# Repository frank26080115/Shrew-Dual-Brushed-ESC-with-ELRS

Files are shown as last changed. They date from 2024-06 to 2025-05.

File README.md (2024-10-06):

# Shrew: Dual Brushed ESC with ELRS

Shrew is family of ESCs (Electronic Speed Controller) that can drive two brushed motors, with an ELRS receiver integrated. It is designed to be as small as possible yet still pack plenty of power. It is meant for insect class combat robots.

There are three variations of Shrew

 * Shrew-Pro, for dual brushed motors up to 21A
 * Shrew-Lite, for dual brushed motors up to 3.7A
 * Shrew-Zero, not a ESC, just a receiver

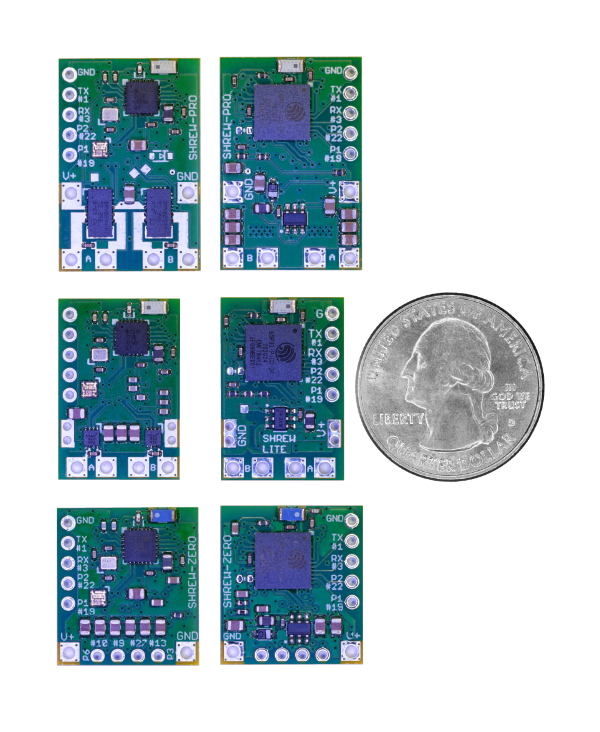
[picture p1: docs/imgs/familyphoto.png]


All of these function as ELRS receivers with 4 or more GPIO pins, capable of controlling other ESCs or servos. These pins can output PWM, as well as better protocols such as Dshot. If you have the skills, you can even use them for I2C and such.

The input voltage ratings of Shrew is incredibly high, even Shrew-Lite can handle up to 36V, that means connecting directly to a 8S battery is not a problem (please see individual detailed specifications).

If you are using AM32 brushless ESCs with Shrew, Shrew features a webpage interface to configure the AM32 ESC. If you have 4 ESCs connected to Shrew, you can change settings on each one individually and test it immediately, all without disconnecting any wires. Plus, you can test the ESCs immediately after making a settings change through the same webpage interface.

## Design Ethos

Safety and reliability is on the top of my priority list

 * Digital protocols are safer than PWM ([why this is better](docs/Digital-Protocols-for-ESC-Control.md))
 * No-pulse failsafe mode by default ([why this is better](docs/No-Pulse-Failsafe-Mode.md))
 * No entering any unexpected modes, there is no way to accidentally enter some sort of calibration mode or binding mode
 * No dead-zone implemented, so there's no control lag at all, and there is also no need for calibration
 * Binding is done with a binding-phrase, extremely good for spare parts management of a competitive robot
 * Power input solder points are intentionally placed farther apart to prevent accidental short circuiting
 * RGB LED on it is indicative of control inputs, not just connection state
 * Top quality TCXO and a ceramic antenna for a balance between high RF performance and durability.

## User Manuals

 * [Shrew-Pro User Manual](Shrew-Pro-User-Manual.md)
 * [Shrew-Lite User Manual](Shrew-Lite-User-Manual.md)
 * [Shrew-Zero User Manual](Shrew-Zero-User-Manual.md)

## Open Source Notes

All of the circuitry is designed using CadSoft EAGLE v7. This is NOT Autodesk EAGLE, but Autodesk EAGLE can open the files.

All the manufacturing data is tailored for JLCPCB's PCBA service.

The firmware in this repo are in binary form only, but the source code for them are on a branch of a fork of ExpressLRS: https://github.com/frank26080115/ExpressLRS/tree/shrew

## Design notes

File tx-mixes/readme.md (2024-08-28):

This is a basic mix setup for a robot being controlled by a EdgeTX RC radio transmitter. It implements a translation between "arcade style" controls to "tank style" drivetrains. It also repurposes the trim adjustments to implement speed limits and rate limits (as opposed to calibrating servos for airplane control surfaces).

The `*.yml` files (for some specific models of radios) I have uploaded can be placed on the microSD card under the `MODELS` directory, rename them to simply `model00.yml` first. Change the number `00` to something else if you need to. If you don't have one of these specific radios, simply take the one most similar to the one you have.

 * [File for RadioMaster MT12](modelnn_mt12.yml)
 * [File for RadioMaster Pocket](modelnn_pocket.yml)
 * [File for RadioMaster Zorro](modelnn_zorro.yml)

To change between using the left stick and right stick, edit the sources in the `inputs` menu.

If you've wired a drive motor backwards, edit the channel direction from the `outputs` menu, select which side and edit the `direction` setting to be `INV`.

Channel 31 and 32 has an `EXPO` curve item set, it's default to 25%. Edit these two curves to fit your needs, 0% means linear.

There are a few logical switches being used by this mix:

 * L57 is the weapon off switch (true = weapon off)
 * L58 is the robot-invert switch, for driving upside-down
 * L56 is the auto-weapon-slow toggle, use this to enable/disable this feature, or temporarily override this feature

The logical switches should be mapped to either phyiscal switches, or be set to a position, using the logical switch panel. (this will make these files more compatible with more radios)

To pick a switch position, set the logical switch to use either `a=b` (true if max) or `a<b` (false if max), with the first parameter being the switch source, and the second parameter being `MAX`. Remember to also set the pre-flight check options for the weapon switch.

There is an intentional slow-up enabled for the weapon channel 3, edit the slowness if you don't need it.

The trim switches are used for real-time adjustments:

 * TrmT, throttle trim: speed scaling for throttle control input
 * TrmE, elevator trim: speed limit for motors, used to scale motor speed up or down after all other calculations
 * TrmR, rudder trim: scaling for steering input, makes the robot turn quicker or slower
 * TrmA, aileron trim: makes one side's motor faster or slower than the opposite side's motor, used to compensate for damaged or binding motor/wheel. If the robot is not driving straight, use this to adjust.

There are a few curves used:

 * CDZ: control dead-zone, implements a dead-zone for the joysticks, can compensate for old joysticks or overly twitchy fingers
   * adjust to fit your needs
 * ADZ: anti-dead-zone, used to avoid any dead-zones implemented on the robot's ESCs, can solve problems with ESCs that appear laggy or unresponsive at low throttle
   * adjust to fit your needs, ask the ESC manufacturer if you have questions
 * P01: positive 0 to 100, a simple line from (-100, 0) to (100, 100)
   * do not adjust
 * P10: positive 100 to 0, a simple line from (-100, 100) to (100, 0)
   * do not adjust
 * WSL: weapon slow, used to automatically slow down a weapon during a steering turn
 * WEP: maps potentiometer/stick to 0 to 100 range, change the range as -100 to 100 if you need to use bi-directional weapon
 * WPS: used by the output stage to apply a offset and multiplication, do not use if the weapon is bi-directional

This mix also includes a control channel for a basic combat robot weapon. Channel 3 is the output for the weapon. Channel 20 is the input for the weapon, using L57 as the switch and potentiometer S1 as the speed control. Channel 3 is set to slowly ramp up the weapon speed, but also brake immedately if the weapon needs to be turned off.

## Notes for MT12

Knob `P2` controls weapon speed, but it is also locked by switch `SA`. This behaviour can be edited.

Weapon speed acceleration has been set to `2.0`, if you want it faster, use the `mixes` page, edit channel 3, change the `slow up` value.

TrmT is T4, TrmE is T3, TrmR is T1, and TrmA is T2

## Notes for Pocket

Knob `S1` controls weapon speed, but it is also locked by switch `SD`. This behaviour can be edited.

Switch `SA` toggles inverted driving mode.

Weapon speed acceleration has been set to `2.0`, if you want it faster, use the `mixes` page, edit channel 3, change the `slow up` value.

## Notes for Zorro

Knob `P1` controls weapon speed, but it is also locked by switch `SE`. This behaviour can be edited.

Switch `SF` toggles inverted driving mode.

Weapon speed acceleration has been set to `2.0`, if you want it faster, use the `mixes` page, edit channel 3, change the `slow up` value.

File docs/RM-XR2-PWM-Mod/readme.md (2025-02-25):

# RadioMaster XR2 Receiver PWM Mod

The RadioMaster XR2 is a nano-sized ExpressLRS receiver. It typically only communicates to a drone flight-controller via two UART pins. Modifying this receiver can allow it to output up to 5 PWM (or even Dshot) signals, which makes it useful for robotics applications.

This is the evolution of the same PWM modification done to many previous generation ExpressLRS nano-sized receivers.

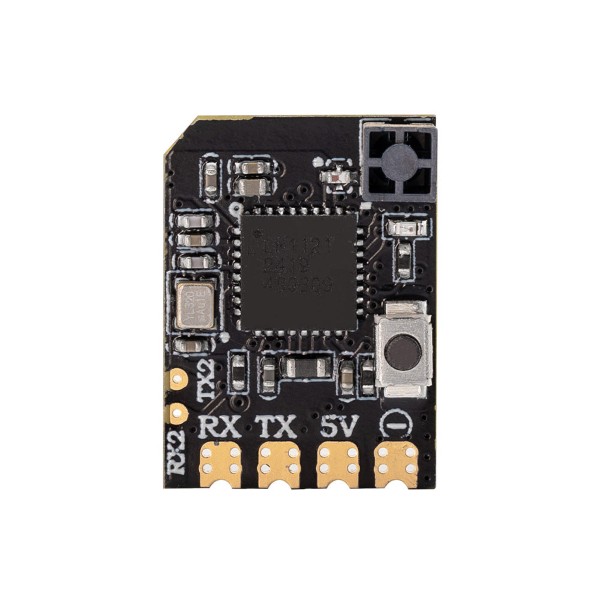
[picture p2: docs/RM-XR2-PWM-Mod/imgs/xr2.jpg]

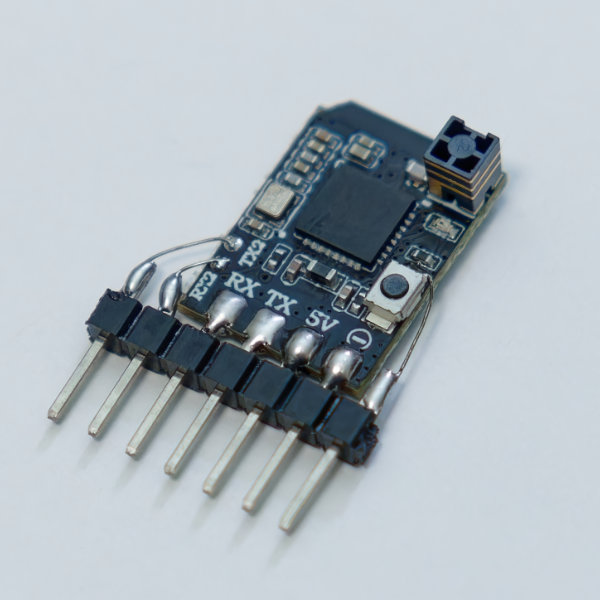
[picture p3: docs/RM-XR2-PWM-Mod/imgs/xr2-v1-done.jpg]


## User Manual

If you have already done the modification, then please read the user manual linked here TODO.

Here's the pin-out for your convenience:

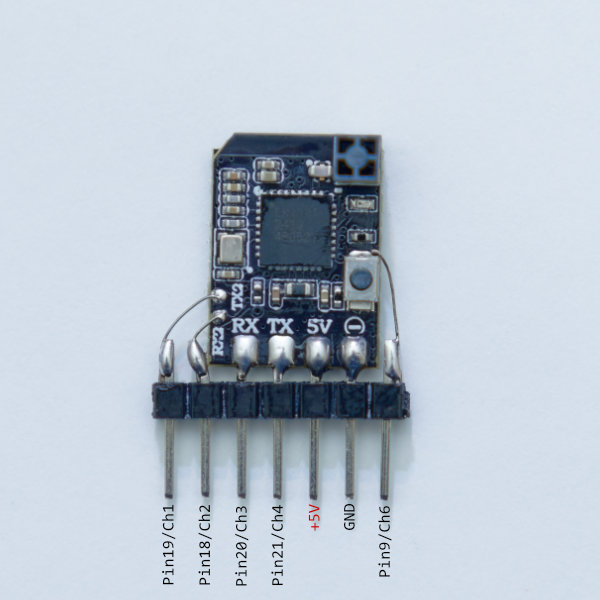
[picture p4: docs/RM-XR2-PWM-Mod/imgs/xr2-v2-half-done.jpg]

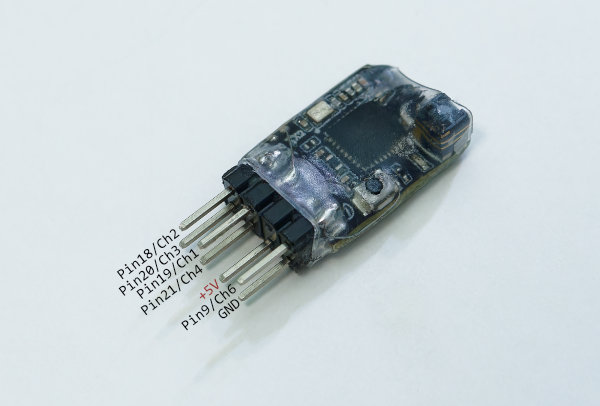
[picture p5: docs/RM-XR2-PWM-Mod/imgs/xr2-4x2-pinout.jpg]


## Method 1: single row of pins

Get a strip of plain male header pins with 0.1" spacing, 7 pins long. Cut and bend the pins according to the photo below:

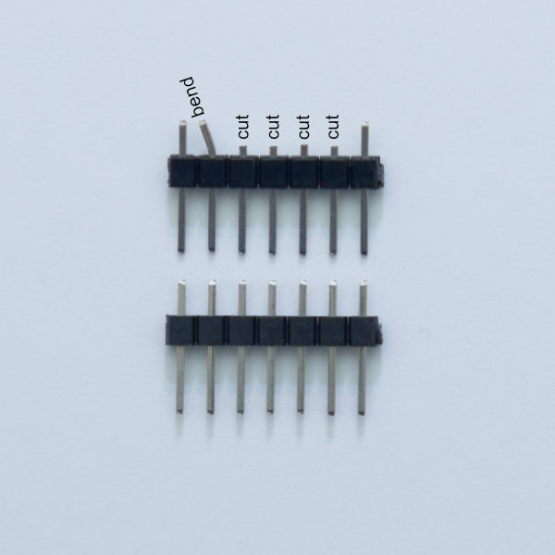
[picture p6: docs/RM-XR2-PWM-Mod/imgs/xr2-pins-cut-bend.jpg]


Solder the header pins to the XR2. Remember to start with just one pin, then adjust it until it is straight, before soldering the four short pins to the castellated pads.

It helps if you stick the male pins into some female headers to keep all the pins straight during soldering. This prevents the pins from moving even if the heat melts the plastic holding the pins.

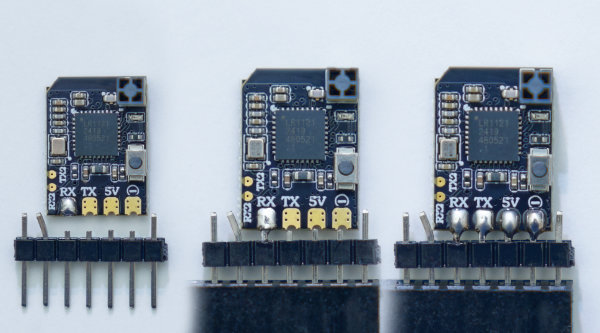
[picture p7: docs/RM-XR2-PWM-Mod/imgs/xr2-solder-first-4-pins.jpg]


Get some thin wire, 30 AWG or 32 AWG solid (not stranded) wire. If you don't have this, maybe take apart some stranded wire and grab individual strands out of it. These wires will only carry a small signal so they don't have to be thick.

Solder one piece of wire to the top solder-pad of the button. The other end of this wire needs to be soldered to the pin on the far right side.

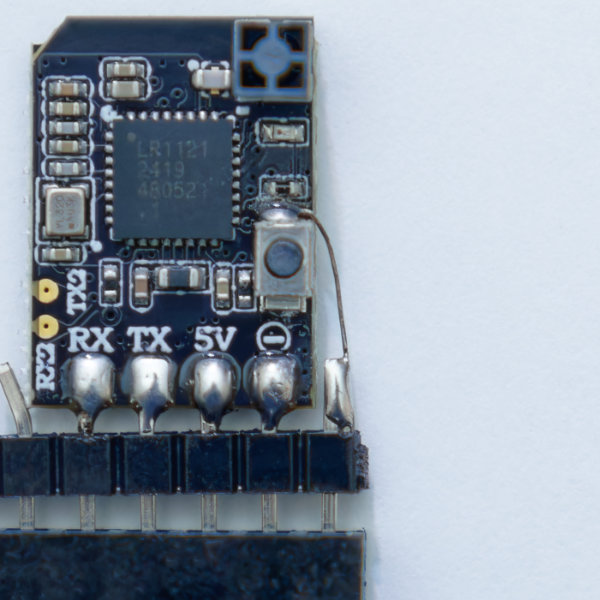
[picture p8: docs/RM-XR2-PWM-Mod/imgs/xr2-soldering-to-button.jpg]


On the left side of the XR2, there are two tiny pads labelled RX2 and TX2. Solder short lengths of wire from those pads to the header pins on the left.

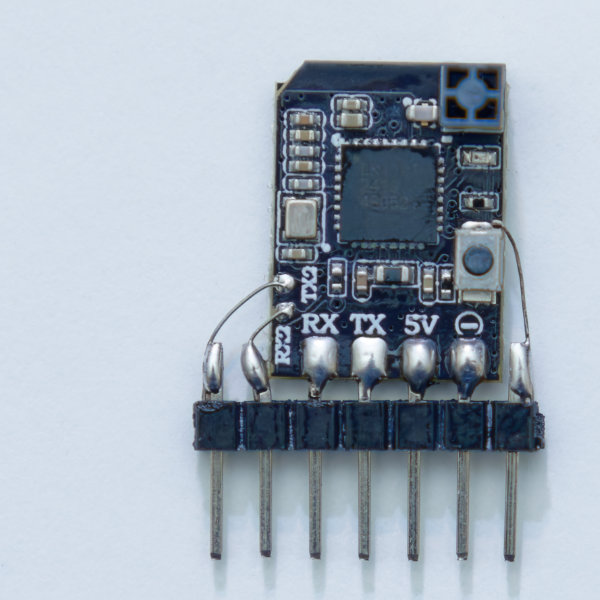
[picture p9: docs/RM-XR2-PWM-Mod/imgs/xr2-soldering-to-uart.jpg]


You are half done. Clean the entire circuit using 99% rubbing alcohol and an antistatic toothbrush. Take a break.



## Method 2: two rows of pins

This method makes the whole receiver narrower. Start by getting a 4x2 chunk of male header pins (0.1" pin spacing). Modify it according to this photo:

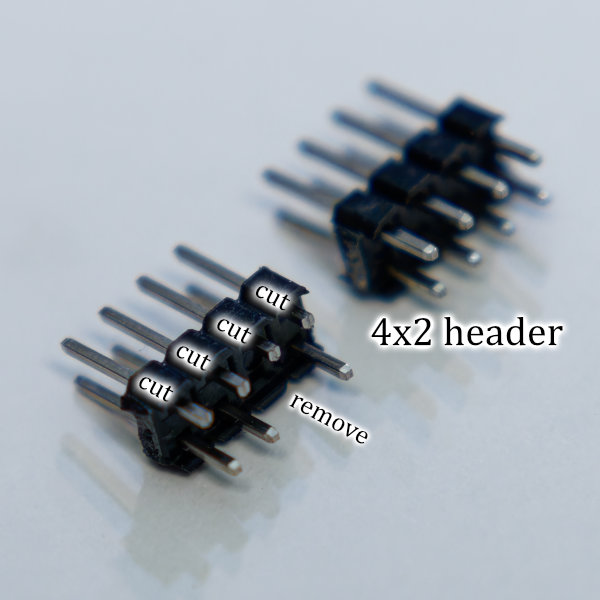
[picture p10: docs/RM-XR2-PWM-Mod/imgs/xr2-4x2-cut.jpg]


Then, similar to the previous method, solder the shorter header pins to the castellated pads on the XR2. The longer pins should be on the higher side.

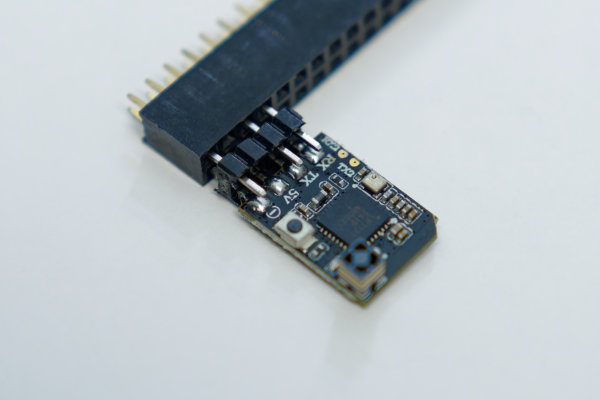
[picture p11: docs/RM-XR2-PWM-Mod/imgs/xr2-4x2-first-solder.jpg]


Make sure there are no unintentional shorts/bridges to the upper row.

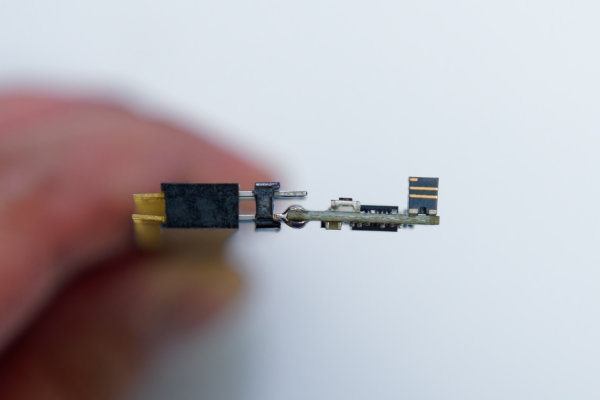
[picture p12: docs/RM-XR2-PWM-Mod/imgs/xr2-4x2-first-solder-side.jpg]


Use thin wire (mentioned above) to connect the top solder pad of the button to the upper header pin on the right side.

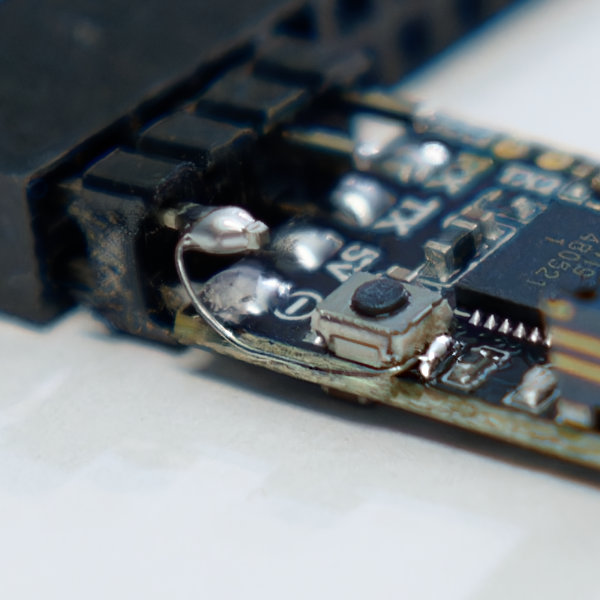
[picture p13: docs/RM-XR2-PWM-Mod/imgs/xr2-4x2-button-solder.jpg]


And then connect the RX2 and TX2 pads to the upper header pins on the left side.

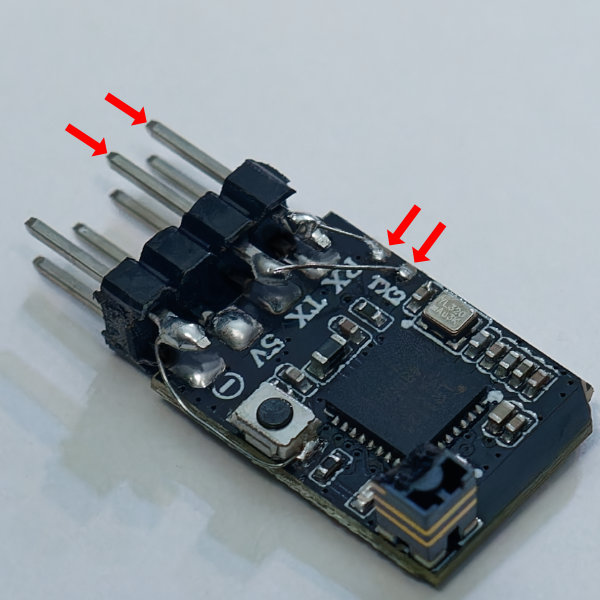
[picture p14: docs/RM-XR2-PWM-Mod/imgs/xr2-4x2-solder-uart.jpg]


Clean the entire circuit using 99% rubbing alcohol and an antistatic toothbrush. Take a break.

## Additional Soldering Notes:

If the wire for the button is too difficult, simply don't attempt it. You will end up with 4 channels instead of 5.

## Protecting Everything

Since we expect this receiver to take a beating, we need to toughen it up because it has a very tall antenna and now some thin wires. Use epoxy to secure the antenna and the thin wires. Then protect everything using heat-shrink tubing.

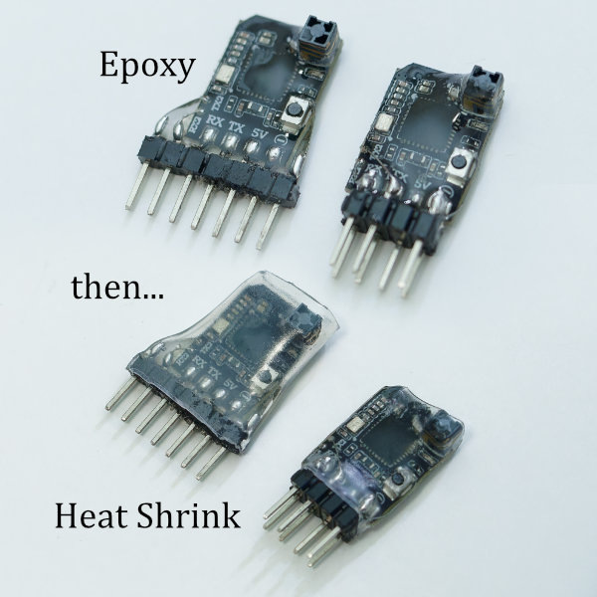
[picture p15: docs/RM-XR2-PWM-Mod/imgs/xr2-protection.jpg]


## Firmware Modification

The real evolution here is that RadioMaster made the XR2 receiver with a more advanced microcontroller, the ESP32-C3. Previous generations of receivers used the ESP8. The ESP32-C3 has more internal features that allows it to send Dshot signals. It can also establish serial communications on any pin, not just the ones labelled as RX and TX.

Dshot is a digital signal that is better than PWM. Since it is digital, it is more resilliant against electrical noise, making it work better with higher voltage power systems.

Since it can communicate using serial on any pin, it means that it can reconfigure AM32 speed controllers (ESC) connected to it, not just one, but as many as you want.

These features are not in the official ExpressLRS firmware yet (today is Feburary of 2025)! Currently Dshot only works with BLHeli32 and not AM32. The AM32 configurator is also not a part of the ExpressLRS project. I have written my own fork of the ExpressLRS firmware that makes Dshot work with AM32 and also adds the AM32 configurator. I have also added a ton of other features specifically tailored towards combat robotics.

Please download the firmware here: [fw-bins directory, pick the latest one](fw-bins)

To update, first get your XR2 into the Wi-Fi mode. Read ["How to get to the Web UI" from this guide](https://www.expresslrs.org/quick-start/webui/#how-to-get-to-the-web-ui).

(Summary: once the receiver is powered ON, wait for 60 seconds until the Wi-Fi interface starts. Connect to the access point named `ExpressLRS RX`, with the password `expresslrs`. There will be no internet available through this access point and your smartphone or computer will need to be told to not disconnect from it.)

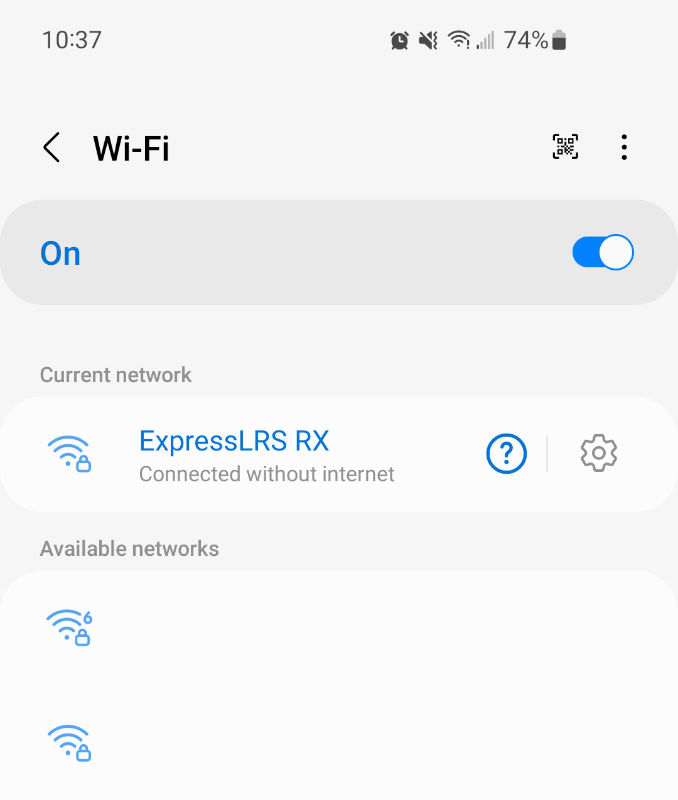
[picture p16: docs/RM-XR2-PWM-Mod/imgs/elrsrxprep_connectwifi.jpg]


Then go to the firmware update tab

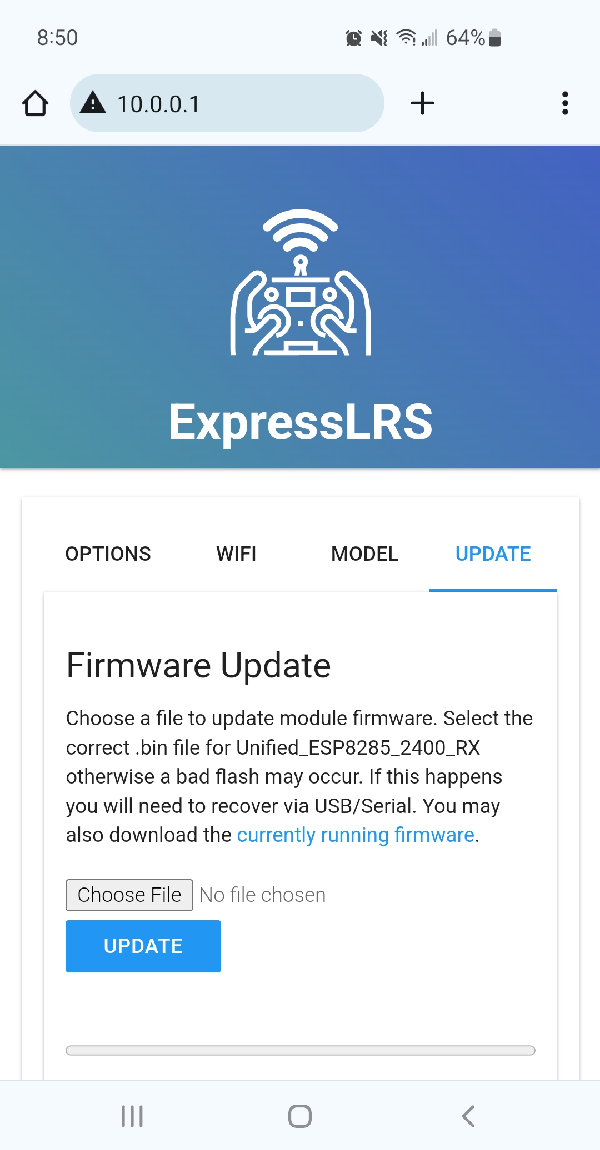
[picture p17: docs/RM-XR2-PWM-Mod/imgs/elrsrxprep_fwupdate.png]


Use it to upload the file I provided. Ignore any warnings and then power cycle.

WARNING: There is bad news, if you own a transmitter that does not support Gemini, then the XR2 is not able to achieve 1000 Hz packet rate, the highest rate will be 500 Hz. If you have your transmitter set to use 1000 Hz, which is the default, then the XR2 will fail to connect.

WARNING: the bind button on the XR2 will not function as a bind button after this mod, so you must bind it with a bind phrase.

List of additiona features that's not in official ExpressLRS release:

 * Dshot works with AM32 and also 3D-Dshot, required for drive motor ESCs that are bidirectional
 * AM32 configurator
 * "Administered" binding mode, prevents accidental loss of binding due to power failure
 * Ability to lock the packet rate to a single frequency, which speeds up the time it takes to reconnect if power is lost
 * Copy settings from one receiver to another
 * Easy for developers to add new features

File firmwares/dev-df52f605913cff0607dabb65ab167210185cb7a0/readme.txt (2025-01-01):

this version adds a boot LED animation that indicates abnormal reasons for reboot

there is also an armed state indication

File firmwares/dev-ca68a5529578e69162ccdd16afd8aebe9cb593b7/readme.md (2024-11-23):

Build from development branch ca68a5529578e69162ccdd16afd8aebe9cb593b7

This version fixes AM32 not responding to DSHOT.

A new DSHOT mode has been added called "Dshot-3D", and it must be used if the ESC is configured for bidirectional rotation (such as for robot drive motors)

Added some minor features to the AM32 configurator:
 * make "complementary PWM" enabled if "bidirectional" is enabled
 * asking if the user wants to switch to/from Dshot-3D if bidirectional is enabled/disabled

Added a mixer for arcade tank drive mixing.

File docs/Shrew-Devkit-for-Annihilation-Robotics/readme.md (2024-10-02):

# Shrew Dev-Kit for Annihilation Robotics

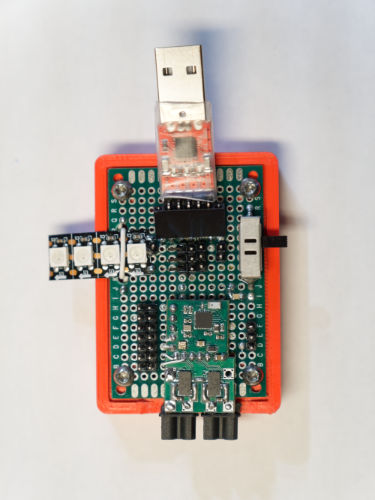
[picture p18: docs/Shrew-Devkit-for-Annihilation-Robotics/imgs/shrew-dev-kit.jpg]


This is a "developer's kit" built using an old retired version of Shrew. It allows for quick repeated updating+testing of Shrew firmware, without having to mess with an actual robot. The serial port is available for updating and debugging. The power comes from the USB port. There are pins that can be connected to external devices.

# Overview

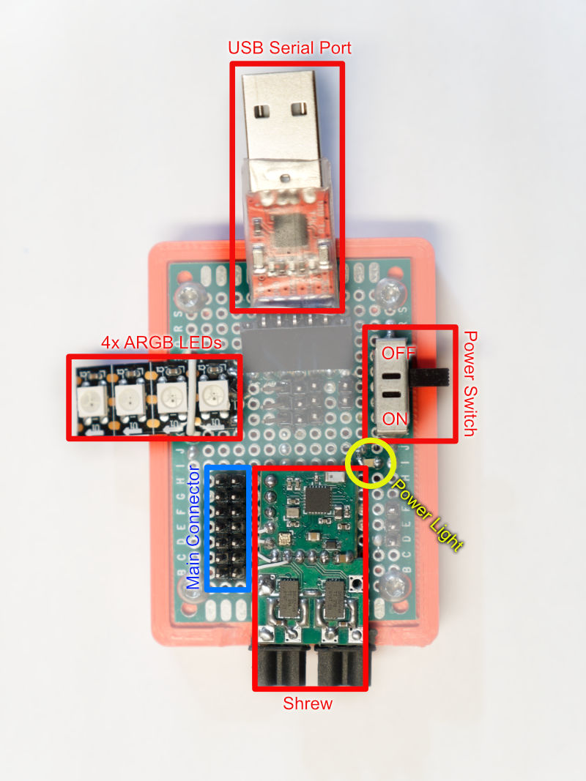
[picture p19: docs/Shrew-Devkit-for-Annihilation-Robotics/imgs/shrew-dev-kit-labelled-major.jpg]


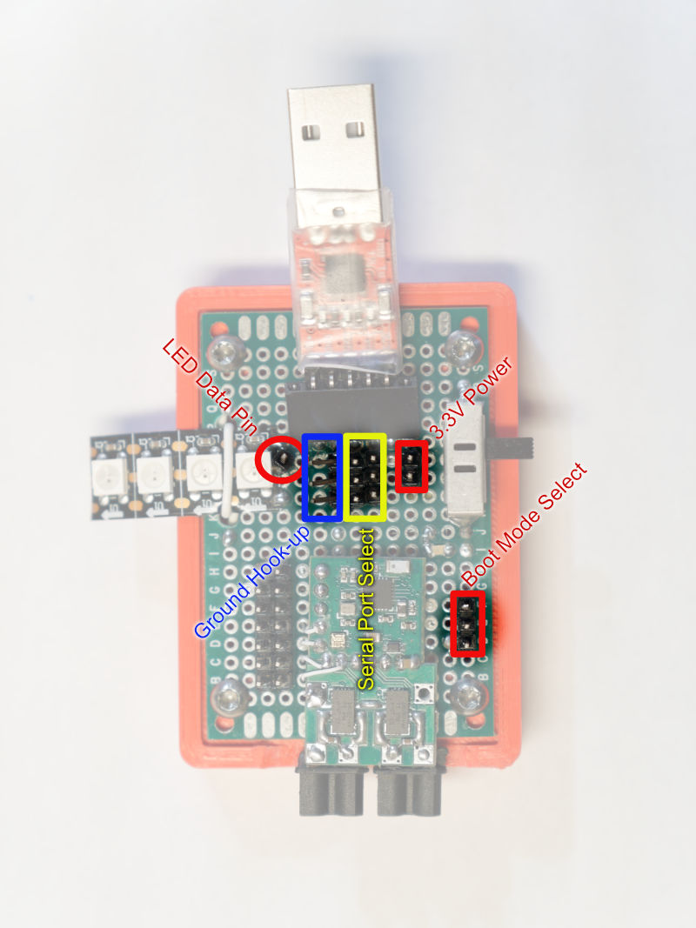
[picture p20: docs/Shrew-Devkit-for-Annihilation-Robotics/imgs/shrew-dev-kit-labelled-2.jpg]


# Pins

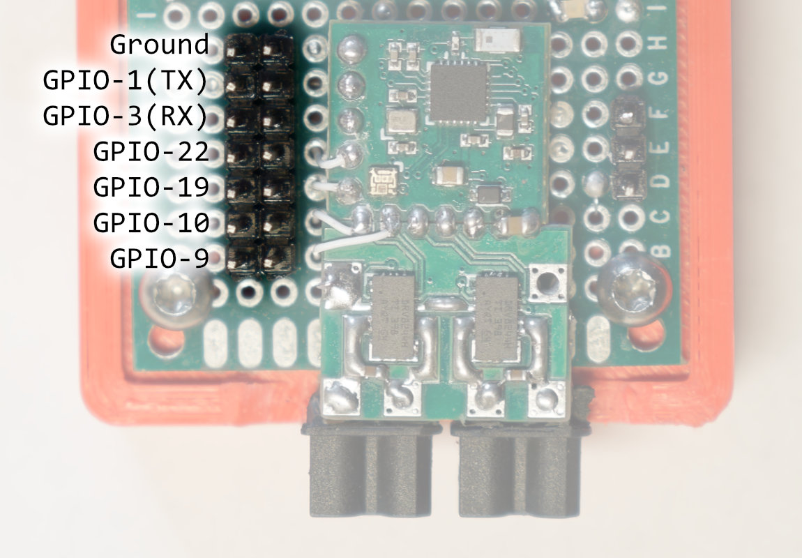
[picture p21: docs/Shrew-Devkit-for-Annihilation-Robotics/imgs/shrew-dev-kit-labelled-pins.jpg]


Each row has two pins, the two are both connected. This can make it easier to connect both an external device and a logic analyzer.

# Shunt Jumpers

Use the included shunt-jumpers to select bootloader mode vs normal mode.

Use the included shunt-jumpers to decide if the USB serial port should be connected or disconnected. If you wish to use the serial port pins for other devices, then move the jumper to the "disconnected"  position so that the USB serial port does not interfer with the external device.

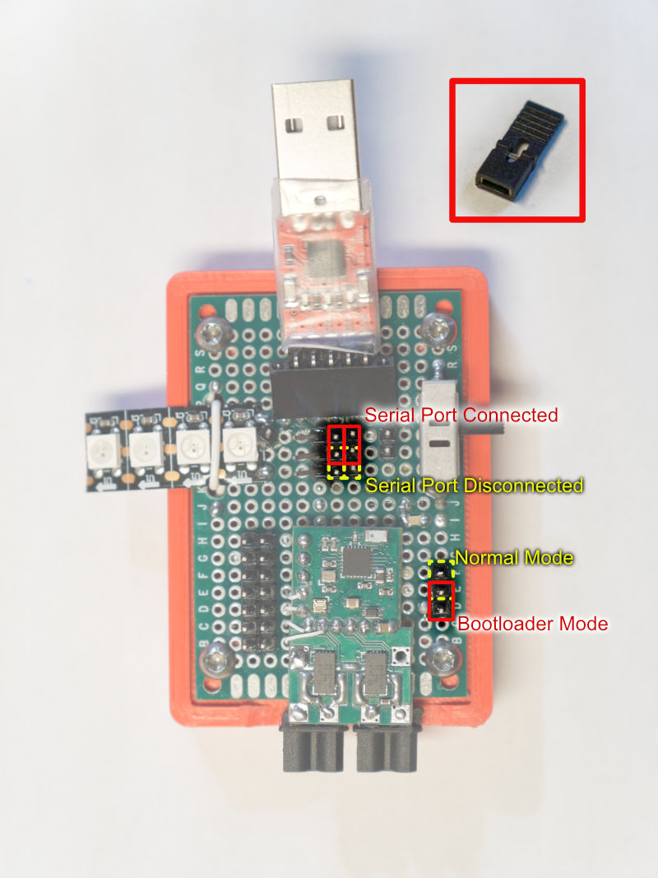
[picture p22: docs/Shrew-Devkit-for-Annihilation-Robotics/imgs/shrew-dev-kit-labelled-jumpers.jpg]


(hint: the yellow positions are meant for you to store the shunt-jumpers so that you don't lose them)

# Using the LED Strip

There is a data pin for the LED strip, use a female-to-female wire to connect that data pin to a GPIO pin on the big main connector. This allows you to pick and choose the pin freely.

# USB Serial port

The connector for the USB serial port is only designed for a particular design I found on Amazon. Please don't lose it. If it needs to be replaced, use this [Amazon product link](https://www.amazon.com/gp/product/B07T1XR9FT/)

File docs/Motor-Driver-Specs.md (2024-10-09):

# Motor Driver Specifications

Shrew-Lite uses DRV8231A motor drivers. Shrew-Pro uses DRV8244 motor drivers. Both of these are integrated H-bridge chips. The datasheets can be [found here (click here)](datasheets-manuals)

## Protection Features

The motor drivers that Shrew uses all feature over-current protection and over-temperature protection. This means, at least according to the manufacturer, they should never allow themselves to be overloaded to a degree that cause them to fail.

Importantly, these drivers also recover from the protected states automatically, and quite quickly.

These protection features are implemented as a shutdown. When the current limit is hit, the chip completely shutsdown, it does not attempt to lower the output to limit the current to a ceiling. Importantly, these drivers also recover from this state automatically, and quite quickly.

The DRV8231A features a very consistent current cutoff, specified at 3.7A. I've tested this with just Gecko motors, which have a stall current only just a little bit over the limit, and it basically refuses to even twitch. This means it's not waiting for much of a "warm up" before kicking in the protection.

The DRV8244's limit is more variable, between 21A and 40A, it is likely temperature dependant. This isn't a bad thing, it allows for more potential performance yet still having a protection when absolutely neccessary. If you analyze the MOSFET resistance of the DRV8244, the variability of the limit might be because it generates such little heat.

If you are building a robot with motors that need the DRV8244s, you will literally melt your motors way before surpassing 21A.

## MOSFET Resistance

All motor drivers have MOSFETs, and while we want to think of MOSFETs as switches, MOSFETs do still have some small resistance. This is actually why MOSFETs heat up when passing current. In fact, this resistance called on-resistance, is probably the most enticing specification that people shop for.

Think about it, the current limit of a MOSFET is actually just a number that will let a MOSFET stay cool enough to survive. The on-resistance is the only thing that causes a MOSFET to heat up. The on-resistance and the ability for the MOSFET to transfer heat away are the two things that dictate what the current limit is. They are all related.

This resistance will also drop the voltage slightly as the current passes through. Your motor will get less voltage after this resistance, which means the motor is weaker. You want the least amount of MOSFET on-resistance to get the best performance out of your motor.

### Example Calculation

Pretend we are using a 12V power source, a motor that draws 3A of current at 12V, and the DRV8231A.

DRV8231A has a on-resistance of 600mΩ

The motor specs suggest its windings have a resistance of 4Ω

The total is 4.6Ω, and when you apply 12V of power and turn the motor driver on, the total current is `12 / 4.6 = 2.6`, 2.6A

Through the MOSFET, that 600mΩ is resulting in, `2.6 * 0.6 = 1.57`, 1.57V loss of voltage going to the motor. Also, it is wasting, `1.57 * 2.6 = 4.08`, 4.08W of heat.

Now, upgrade to a DRV8244, which features a 47mΩ on-resistance (Excuse me? It's that low? YES! This chip represents a technological leap in MOSFET manufacturing technology)

The total current is `12 / 4.047 = 2.965`, 2.965A

The loss through the MOSFET is `2.965 * 0.047 = 0.14`, 0.14V. And the wasted heat is `0.14 * 2.965 = 0.41`, 0.41W.

This means the DRV8244 can give you 13% more torque and speed than the DRV8231A when using the same motors and same input voltage.

This also means you can drive a motor roughly 10x more powerful with the DRV8244 and still get the same heat output as a DRV8231A. The DRV8244 is bigger physically as well so it can handle more heat because of that too.

For fun, consider the L298N motor driver, which was popular when I was a kid, and is still being sold today. It uses classic BJT transistors internally instead of MOSFETs. It's specified to handle 45V inputs and a current of 4A, which is quite respectable on the surface. But if you read the datasheet closely, you'll see that the on-resistance is about 2Ω, which is insanely high. Motors will run much slower with it and the driver is gigantic physically to dissipate the wasted heat.

Despite me raving about the DRV8244's advantages, the DRV8231A is not bad, it's quite good for its size and its price. It's lovely compared to the junk you might encounter that don't tell you what motor driver you are actually getting.

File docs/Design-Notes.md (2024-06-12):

# Microcontroller

The ESP32-PICO-D4 chosen, because ExpressLRS supports it. The AnyLeaf designs uses it https://github.com/AnyLeaf/elrs-hardware/

It has internal flash memory and no PSRAM.

The circuit design has taken into consideration all of the pin bootstrapping.

The SPI bus used to connect the SX1280 uses arbitary GPIO pins selected for convenience during PCB layout. Research indicated that the ESP32 can map any pin to any SPI bus function as long as only one SPI bus is being used. (if both VSPI and HSPI are being used, then you must use the specific pins assigned to both VSPI and HSPI)

The RF antenna is attached directly to the ESP32 LNA pin without any filtering or matching circuit. This is because the Wi-Fi functionality of the ESP32 is only used during reconfiguration and it will always be in close proximity to the user's smartphone.

# Radio

`SX1280IMLTRT` is used, because it is pretty much the only thing used for ExpressLRS in the 2.4GHz band.

It is configured to use DC-DC power mode, not the LDO mode. I have not found any example designs using LDO mode and I also don't see any advantage to using LDO mode.

`2450FM07D0034` is an all-in-one ceramic filter connected to the SX1280 before the antenna.

The SX1280 requires a 52MHz oscillator, ideally a temperature compensated one. The Seiko Epson `X1G0054410320` has been selected due to it's low cost and small size.

RF performance is not super critical. Most ExpressLRS receivers are meant for long range aircraft flight. For combat robotics, the range required is only a few feet at most.

# Motor Driver: DRV8231

`DRV8231ADSGR` is a tiny motor driver capable of up to 3.7A of current and can handle 33V of input voltage.

It features overcurrent protection. When the current limit is hit, it will disable itself for 3 milliseconds. It also features undervoltage-lockout and thermal shutdown.

Either the DRV8231 or the DRV8231A can be used in the design as current regulation is not being used at all.

https://www.ti.com/product/DRV8231A

https://www.digikey.com/en/products/detail/texas-instruments/DRV8231ADSGR/15854016

# Motor Driver: DRV8244

`DRV8244HQRYJRQ1` is capable of driving 21A of current and handle up to 35V of input voltage. The internal resistance of this driver is incredibly low at about 47 milli-ohms. In theory, this driver will run cooler than the DRV8231 for my use case.

The QFN footprint is selected. And the HW variant is chosen so that a SPI bus is not required for configuration.

This driver features over-current protection and over-temperature protection. It is configured to automatically retry when a fault is detected. The retry time is under 1 millisecond.

https://www.ti.com/product/DRV8244-Q1

# Voltage Regulator - Mini

`AP7375-33Y-13` https://www.digikey.com/en/products/detail/diodes-incorporated/AP7375-33Y-13/20371309

Rated for 45V and 300mA. Features thermal protection.

I don't expect any users to exceed 18V.

# Voltage Regulator - Mega

`LT1129CST-3.3#PBF` https://www.digikey.com/en/products/detail/analog-devices-inc/LT1129CST-3-3-PBF/889181

`MIC5239-3.3YS-TR` https://www.digikey.com/en/products/detail/microchip-technology/MIC5239-3-3YS-TR/1030750

These LDO voltage regulators have a decent rating and also require low valued ceramic capacitors.

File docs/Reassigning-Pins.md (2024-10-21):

# Assigning PWM to Serial Pins

Shrew comes with serial RX and TX pins assigned to work as a CRSF port by default. These pins can be reassigned to be more PWM or Dshot pins.

There are two ways of doing this, the easiest way is to edit the hardware configuration through the Wi-Fi interface. Activate Wi-Fi mode (see your specific user manual), connect to it, and then visit the page at `http://10.0.0.1/hardware.html`

On this page, you'll see pin function assignments that can be edited with a text-box. Find the `RX pin` and `TX pin` text-boxes, and delete their contents, make sure they are blank. Then, find the text-box for `PWM output pins`, and add the numbers `, 1, 3` to the list.

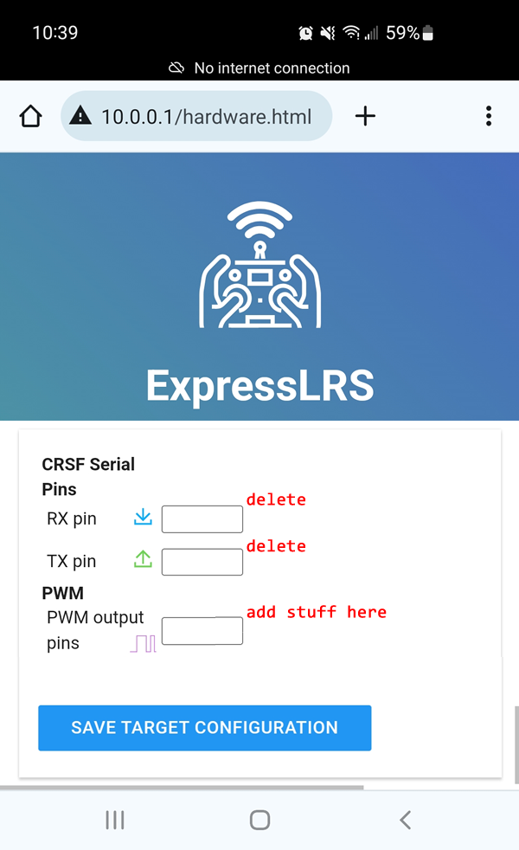
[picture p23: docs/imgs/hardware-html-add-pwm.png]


Save your configuration, and then reboot Shrew completely.

When Shrew powers up again, activate Wi-Fi mode again, connect to it, and then visit the main page at `http://10.0.0.1/`. Now is the time to make sure the PWM channels are configured correctly.

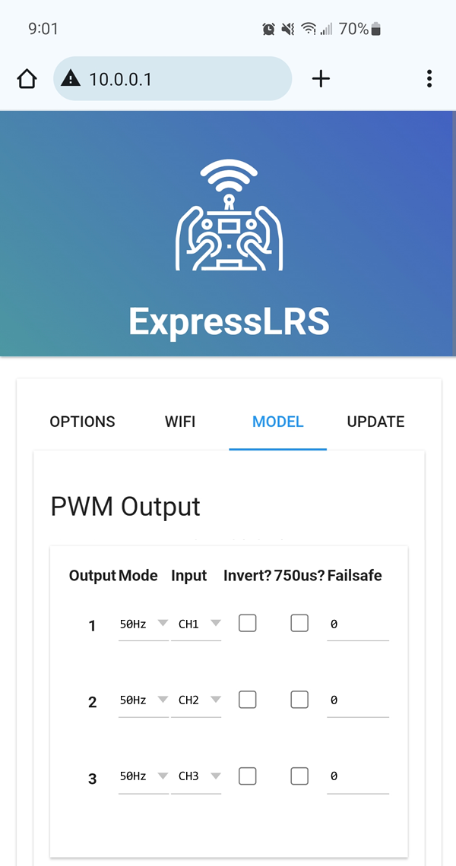
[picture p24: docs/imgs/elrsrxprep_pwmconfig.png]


Make sure to save at the end.

**IMPORTANT:** If you want to change a PWM pin back into a serial pin, make sure you remove it from the list of PWM pins. If you are doing some advanced hacking, you probably don't want your pin to exist in any of the lists where it's not supposed to be in.

## The Other Method

Read the [development guide](Development-Guide) to see how to edit the hardware JSON files, which will become a part of a new firmware file if you rebuild the firmware. The entries in the JSON file for `serial_rx` and `serial_tx` must be blank, and then the pins `, 1, 3` must be added to the `pwm_outputs` array.

## Other Pins

The bootloader mode activation pin is pin 0, and it actually can be used as an output pin.

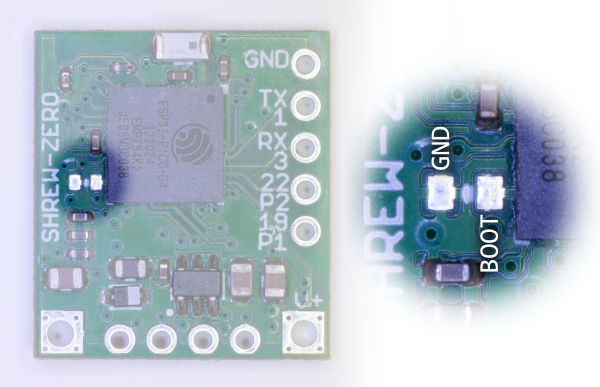
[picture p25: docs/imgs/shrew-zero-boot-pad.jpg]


However you must be careful that whatever you connect doesn't cause the bootloader mode to be activated unintentionally. This means, whatever is connected to this pin must be either pulled-up or floating (aka high-Z or high-impedance).

On a Shrew-Pro, there is a pad to access the reset signal for the SX1280 and DRV8244.



This is pin number 21. You cannot modify this pin's function but you can take advantage of its reset pulse. It will always pulse a low signal for exactly 10 microseconds when the ESP32 is initializing.

## 3.3V Power

You can obtain a source of 3.3V power by soldering to this capacitor:



(this capacitor exists on all variations of Shrew)

The power supply is not very powerful, the rating of the voltage regulator is about 600mA, you should assume that Shrew already uses about 100mA during normal operation, and 250mA during Wi-Fi mode.

You can use this to implement a small IMU sensor as an example.

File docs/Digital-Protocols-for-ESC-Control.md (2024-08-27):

# Digital Protocols for ESC Control

## Understanding PWM

Traditionally, RC radios sent control signals as pulses. A long pulse tells a motor to speed up, while a shorter pulse tells the motor to slow down or stop.



This is called Pulse Width Modulation, or PWM. This was the standard because the RC radio hobby is older than computers, and this was the easiest, cheapest way.

But this type of signaling has many disadvantages. It is an analog form of communication, not digital. The device generating the pulse might have wanted to generate a pulse that's 1.234 milliseconds long, but because of non-idealities of the real world such as temperature and stray capacitance, it might've generated a pulse that's actually 1.235753 milliseconds long. The device reading that pulse is also subject to non-idealities, and read the pulse as 1.237598 milliseconds.

This isn't such a big deal since we have techniques such as trimming, and it is also why almost all ESCs have a calibration function. But these methods do not solve the problem of having noise in the PWM signal.

Below is a simple diagram to illustrate how some noise can cause a motor to unintentionally start spinning, which is a safety concern.



Next, this scenario will make a motor to stutter while it is spinning.



The motor ESC that's reading the PWM signal cannot really distinguish between what is noise and what is a true signal.

## Digital Signals

When a signal is called digital, it means that the information is being sent as **discrete** symbols. When the transmitter sends 123, the receiver receives exactly 123. In that example, the number 123 is encoded as a series of binary bits, ones and zeros, 1 and 0.

These binary bits are still being sent as electrical pulses.

The Dshot protocol sends the 1 bit as a long pulse and the 0 bit as a short pulse. The difference between a long pulse and a short pulse in this context is quite large so it is extremely difficult to confuse between a 1 and 0.



The CRSF protocol is following a standard serial port encoding. 1 is sent as a high voltage and a 0 is sent as a low voltage. The bits are sent in series, each bit taking the same time no matter what. The receiver has to simply read the voltage at regular time intervals. The first bit is always 0, and the last bit is always 1, and the number of bits is always 8. This way, the receiver knows when to start reading.



## Data Integrity Checks

While digital protocols are very resistant to things like temperature changes, they are not immune to noise. Depending on the strength of the noise, a 0 can be turned into a 1.

Digital protocols like DShot and CRSF feature a data integrity check, implemented as a CRC (cyclic redundancy check) checksum. Data integrety checks are what's used to ensure a packet of data, or a file, is not corrupted. The checksum bits are sent after the data bits, and represents a mathematical calculation that can prove the data bits have not been corrupted.

For example, let's pretend to use a protocol that sends 4 numbers and uses 1 number as a simple checksum that sums up all four numbers. We send `34, 57, 19, 24` as the data, 34 + 57 + 19 + 24 = 134, so the final packet looks like `34, 57, 19, 24, 134`. But if because of noise, the 57 is corrupted into 58, then the receiver reads a packet that looks like `34, 58, 19, 24, 134`. The receiver performs a checksum calculation 34 + 58 + 19 + 24 = 135, since 135 is not 134, the receiver knows that the packet is corrupted, and it is ignored.

NOTE: the CRC checksum algorithm is a bit more complicated than just addition.

The data integrity check feature is extremely good for safety and reliability. The diagrams below shows what happens if the noise occurs between packets, or even during a packet.



If the noise happens when no packet is being sent, the noise does not look like a packet with a correct checksum, so nothing bad happens. If the noise occurs right in the middle of a packet, the packet is also simply rejected, due to a bad checksum, instead of causing the motor to behave unexpectedly.

As a reminder, if the noise happens to a PWM signal, it might appear as a longer PWM signal than what it should be, causing a motor to spin up unexpectedly.

Therefore, it is much safer to use a digital protocol that has a data integrity check, such as DShot or CRSF.

## The Relevant Protocols

The most relevant digital protocols for us are: DShot, CRSF, and SBUS. These are used in RC hobbies such as multicopters. Shrew is here to also use these protocols for RC hobby robotics.

### Dshot

DShot is used to control a single ESC. When hobby multicopter microcontrollers (flight controllers, aka FC) became more capable, DShot was invented to provide more precise and more reliable control of brushless motor ESCs.

On Shrew, all pins can be configured to use DSHOT300, where the 300 indicates the bit-rate. This protocol is accepted by all BLHeli_S, BLHeli_32, and AM32 firmware ESCs.

There are no extra configuration needed on the ESCs to use DShot, it should be automatically detected.

Because each DShot signal only connects to one ESC, when Shrew is connected to multiple ESCs with DShot, each ESC can be individually configured through the web-ui. When using Shrew, DShot is the recommended method of connecting to ESCs.

### CRSF

CRSF is a protocol used to communicate between a RC radio receiver and a flight controller, the flight controller is expected to take data from a CRSF packet, and then split it to DShot packets for the four ESCs typically used in a quadcopter. But today, ESCs running AM32 can decode CRSF directly instead of requiring a flight controller.

(NOTE: only the cutting edge experimental AM32 firmware can decode CRSF right now, the official regular AM32 firmware cannot, we are all waiting for the experimental features to be added to the official features. It is easy to upgrade older AM32 firmware to the newer experimental firmware)

A CRSF control packet can carry multiple channels of data at once. This means one output pin on the receiver can control multiple ESCs at once. This requires each ESC to be configured to use CRSF and also configured to know which sub-portion of the whole CRSF packet it should be reading.

Shrew sends CRSF out the UART-TX pin by default. This pin can be reassigned as a PWM or DShot pin if you don't need it.

Because while using CRSF, all the ESCs have to use a single pin, the ESCs **cannot** be configured at all while connected to the receiver.

### SBUS

SBUS is similar to CRSF, it is the standard used by FrSky brand products. ESCs running the latest BLHeli_32 firmware can decode SBUS. FrSky intentionally made SBUS difficult to use by DIY electronics hobbyists, in order to drive more sales of their own products. Hence it is not as popular.

Shrew is capable of sending SBUS. The protocol needs to be reconfigured from CRSF to SBUS through the web-ui. The baud rate also needs to be changed to 100000.

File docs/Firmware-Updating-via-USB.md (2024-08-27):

# Firmware Updating via USB

## Preparing the Circuit

The Shrew circuit has a `BOOT` pad on it, next to it is a ground pad.



To place it into bootloader mode, solder something between the boot pad and the ground pad. It's quite easy to bridge the two pads with just a single blob of solder, but an alternative is to use a thin piece of wire.



## USB to Serial Converter

You will need to have a USB-to-serial converter of some sort.



There are a lot of options. My personal preference is to get something from SparkFun Electronics

 * [SparkFun Serial Basic Breakout - CH340C and USB-C](https://www.sparkfun.com/products/15096)
 * [SparkFun Serial Basic Breakout - CH340G](https://www.sparkfun.com/products/14050) (USB-micro)
 * [SparkFun Beefy 3 - FTDI Basic Breakout](https://www.sparkfun.com/products/13746) (this one claims to handle more power on the 3.3V bus, but costs 2x as much)
 * [Amazon product link](https://www.amazon.com/dp/B07T1XR9FT) (it's a pack of 4 for about $10)

For whichever one you get, plug it in to your computer and install the appropriate driver for it.

If the voltage on the converter can be changed, make sure it's set to 3.3V

## Connections

**IMPORTANT:** make sure the boot pad is already grounded!!!

Make the connections like so



Notice that the TX pin on the converter connects to the RX pin on the Shrew. The RX pin on the converter connects to the TX pin on the Shrew.

## Flashing

If you are using the online firmware configurator tool at [https://expresslrsconfig.eleccelerator.com/](https://expresslrsconfig.eleccelerator.com/) then you should be able to click "Flash Firmware". You will be prompted to select a serial port, select the one representing your USB-to-serial converter.



If you are using PlatformIO (if you are building from source code), then get to the PlatformIO tab, select `Unified_Shrew..._via_UART` as appropriate, select the serial port at bottom of the screen, and then click `Upload`.





**IMPORTANT:** if you need to do a recovery of some sort, it might be wise to also perform a full flash erase. For PlatformIO, the option for `Erase Flash` is tucked under the `Platform` option group.

**IMPORTANT:** Do not use the official ExpressLRS configurator. It does not provide the customized firmware version that Shrew requires.

## Remove the BOOT Jumper

After you finished flashing, remember to remove the solder jumper you put on the `BOOT` pad. Or else the Shrew will never power up into normal mode, it'll be stuck in bootloader mode until you remove that jumper.

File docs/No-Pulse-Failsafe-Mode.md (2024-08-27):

# No-Pulse Failsafe Mode

ExpressLRS features a failsafe mode called "no-pulse", which means that if the radio transmitter is disconnected somehow, the ExpressLRS receiver sends absolutely no signals to connected ESCs at all.

This is different from other RC radio receivers, where you set a specific pulse width that is to be sent when the radio transmitter is disconnected. This is called "set position" inside ExpressLRS, as ExpressLRS allows you to pick between three different failsafe modes.

The "set position" failsafe mode is not very safe when it is used in a hobby robotics context.

First, understand that ESCs typically require an **arming** signal before it will spin a motor. The arming signal is a signal that tells the ESC to stop spinning. This is supposed to ensure that the motor never starts spinning as soon as the user turns on the power switch. If the user left the throttle on the radio transmitter in a high position, and then powered-on the robot, it does not immediately start spinning the motor.

The problem is if the failsafe signal is also the stop signal, then that means the failsafe signal is also the arming signal. Disconnecting a radio transmitter will also arm the ESC, maybe without the user even realizing. If the user powers-on the robot but leaves the radio transmitter off, then the receiver will arm the ESC, and then if the user powers-on the radio transmitter next with a high throttle, then the motor will unexpectedly start spinning.

In contrast, when a no-pulse failsafe mode is used, then the **ESC will never arm unless both the radio transmitter is already powered-on and also the throttle is actually low**. And if the signal is lost, the **ESC will go back into an disarmed state**, waiting for another arming signal.

Also, with bidirectional ESCs using PWM, it is possible for high temperatures to cause the failsafe position to actually be misinterpreted, and then the motor will unexpectedly start spinning with no way of shutting it down. The no-pulse failsafe mode will prevent such incidents from happening.

While it is possible to configure most radio transmitters to warn the user if the transmitter has a high throttle when booting up, it is simply not reliable to expect the user to... actually do anything, even getting a user to read a manual is pretty hard (thanks for reading, by the way). These are also often kids. Thus, the Shrew is configured to use no-pulse by default.

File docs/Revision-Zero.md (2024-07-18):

# Revision Zero

The first batch of prototypes were made around June of 2024. This batch is special and different from subsequent batches.

All PCBs are made without castellated edge holes to save cost. This makes the PCB a bit bigger than intended. To join the receiver and motor driver PCBs together, the edge of the PCB can be sanded down first to create castellated edge holes that are soldered together.



The receiver PCB half is manufactured as a standard 4 layer PCB with 1 oz copper. The mini motor driver PCB is made with a 2 layer PCB with 1 oz copper. The mega motor driver is made with a 2 layer PCB with 2 oz copper. Any future revisions with the two halves integrated will need to use a 4 layer PCB.



I forgot to put some silkscreen text on the PCBs. Please refer to diagram to avoid any wiring mistakes.

The footprints being used for the 0402 components are a bit larger than what the PCB manufacture prefers, but this might help me when I am hand soldering or doing repair work. Future revisions will have a smaller footprint for the 0402 components.

## Botched Signals

The receiver portion has a pin assignment error. I had JLCPCB put in the ESP32-Pico-D4, the first generation of the Pico, but on that particular chip, the pins for GPIO16 and GPIO17, which are wired for the motor drivers, cannot be used at all. So to fix this, I've used some bodge-wiring to connect those to GPIO9 and GPIO10 instead (these were supposed to be auxiliary servo signals).

This means revision-zero loses two pins for auxiliary servos, and probably cannot do things with I2C or CAN bus. The serial TX and serial RX pins can in theory be used for other purposes other than serial port though.

The Shrew-Mega motor driver PCB is missing the sleep signal. The design tied the sleep signal to 3.3V but this is apparently never going to work, the DRV8244 chip requires a very brief low pulse on the sleep signal before it works. So to fix this with a bodge-wire, the voltage regulator's output leg is bent and connected directly to the Shrew-RX's GPIO4 (this used to be the battery measuring ADC pin). The existing 3.3V signal is rerouted to the Shrew-RX's RX pin.

## Mini Motor Driver

The components for revision-zero may differ from future cost optimized revisions.

The voltage regulator is a [DS8242-33A3L](https://jlcpcb.com/partdetail/Dstech-DS824233A3L/C5884130), which is rated for up to 23V input continuously, 28V absolute maximum. It claims to output 500mA continuously when not considering thermal derating. It does feature thermal limiting. Dropout voltage is 0.5V.

The input capacitors on this circuit are four [C440198](https://jlcpcb.com/partdetail/439567-GRM21BR61H106KE43L/C440198), 10uF 50V X5R +/-10% ceramic capacitors. Future revisions may aim to use capacitors that have higher capacitance.

## Mega Motor Driver

The revision-zero mega variant motor driver is completely hand soldered.

The voltage regulator on it is a [MIC5239-3.3YS](https://www.digikey.com/en/products/detail/microchip-technology/MIC5239-3-3YS-TR/1030750). It is rated for a 30V input, 32V absolute maximum input. It claims to output 500mA continuously when not considering thermal derating. It does feature thermal limiting. Dropout voltage is 0.35V.

The input capacitors on this circuit are 7x [C2012X5R1V226M125AC](https://www.digikey.com/en/products/detail/tdk-corporation/C2012X5R1V226M125AC/3951664), 22uF 35V X5R ceramic capacitors. These are somewhat expensive and may not be used in future cost optimized revisions.

# Oscillator Quality

The oscillator is a TCXO, temperature compensated crystal oscillator. This type of oscillator should ensure that the RF performance is superb under all temperature conditions. The particular part being used is a `Seiko Epson X1G0054410320`.

ExpressLRS has a test mode that generates a continuous wave at 2440 MHz and you are supposed to measure it to see how good your oscillator is. The lower the deviation from 2440 MHz, the better. More information about this test: https://www.expresslrs.org/hardware/crystal-frequency-error/



It's measuring a 2440.006 MHz in the above screen shot, which is about as good as it gets.

## Initial Thermal Tests on Voltage Regulator

Test condition:

 * PCBs are detached
 * Input voltage 17.2V
 * Room temperature set to 75°F, which is 24°C
 * Receiver is connected to Transmitter, 100Hz packet rate, 10mW telemetry, 1:32 telemetry ratio. This is roughly 120mA of load on the 3.3V power

Voltage Regulator `MIC5239-3.3YS`



Voltage Regulator `DS8242-33A3L`



ESP32-Pico-D4



SX1280



## 2nd Thermal Tests on Voltage Regulator

 * Same setup as above
 * Receiver is connected to Transmitter, 100Hz packet rate, 10mW telemetry, 1:128 telemetry ratio. This is roughly 80mA of load on the 3.3V power

Voltage Regulator `MIC5239-3.3YS`



Voltage Regulator `DS8242-33A3L`



## Thermal Test on Shrew-Mega

 * 12V input
 * Driving two JCR Viper motors, with gearbox, without load
 * Measurements taken after 5 minutes of running

The steady-state current drawn by these two motors started off at about 1.1A combined, and slowly tappered off to about 0.7A combined, which I think is because of the internal resistance of the DRV8244 increasing slowly as temperature also rose.

Side with motor drivers:



Side with voltage regulator:



## Thermal Test on Shrew-Mini

 * 12V input
 * Driving 2x2 N20 motors, with gearbox, without load
 * Measurements taken after 5 minutes of running

The steady-state current drawn by these four motors started off at about 0.37A combined, and slowly tappered off to about 0.29A combined.

Side with motor drivers:



Side with voltage regulator:



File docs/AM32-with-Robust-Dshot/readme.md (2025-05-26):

# AM32 with Robust Dshot

## What is Dshot

Dshot is a digital communication protocol used in RC hobbies, most prominently in drones, for a flight controller to tell a speed controller how fast to spin. It's way better than any of the usual PWM methods, it's quick to send, it's precise because it's digital, and it's safe because it's protected by a CRC.

Dshot is better than CRSF because each ESC can be individually configured. If a bunch of ESCs are using CRSF, you need to disconnect a ESC every time you want to reconfigure it. With Dshot, you just leave them all connected and you can still reconfigure all of the ESCs.

## The Issue

This is written on May 5 2025. There's a chance that the issue below has been addressed, especially since I've brought the issue and solution to light.

When Dshot is used in a high noise environment, AM32's method of receiving Dshot packets has a chance of getting in a state when it rejects a ton of packets. Let me explain...

AM32 receives Dshot by measuring 16 pulses, which is 32 signal edges. When the DMA receives 32 timestamps from the input-capture-timer, it executes the evaluation function, then the DMA is reset back to 0.



So what happens when there's a noise spike?



The above diagram is how the main developer of AM32 told me what would happen.

Notice how the time it takes to "read" is longer than the time for one pulse?



The reading function does take some time to execute, it has to calculate if each pulse is a 1 or 0, and then do a CRC calculation.



So in the event of a singular noise spike, everything should work fine but we lose one packet, the next packet is still fine. In fact, if this is true, then even if we have more than one noise event, it might reject one or two packets, but it will **eventually recover** to a normal state again.

Or... so we thought...

The code also does something else clever. It measures the time between the first pulse and last pulse, and if it's too long or too short, it rejects the packet.



This is quick, great, being quick does mean higher possible RPMs for the motor. BUT it means the reading function is extremely fast when it detects an error. It only does one subtraction operation, instead of all the iteration and CRC stuff.



We then end up with missing consecutive packets even though we only had one noise spike.



I've experienced this both on the bench tests and also during a robot fight when the two robots did a weapon-on-weapon hit. My robot ended up with a unresponsive weapon after that event, it was getting a signal, there's a way to tell, but it wasn't getting a valid signal.

## My Solution

Instead of having the DMA count to 32, I'm using it's half-way feature and it's circular buffer feature. I can tell it to count to 64, but also run a event when the count gets to 32. Also, if it goes over 64, the DMA automatically resets to 0 and continues recording (instead of relying on some code to finish first and then being reset manually).

Now I have 64 signal edges remembered, so 32 pulses, which is 2 packets of Dshot. My algorithm scans, from the latest pulse, backwards, looking for a complete and valid Dshot packet.

It is guaranteed to find at least one packet that's valid. In a noiseless scenario, it will be memorizing 2 completely valid packets but only evaluate the latest one.



I pointed out a flaw in this, which is that noise will cause a slight lag. For combat robotics, this lag is negligible. For racing drones? I'm not sure. There's a few solutions to remove the lag but they are kind of complicated. Such fixes will require people with more experience around drones and plenty of real world testing.

## Availability

Before you start, obviously you need to be using something that sends Dshot. If you are using Shrew, you already have it. [If you are using a RadioMaster XR2, then you need my special firmware that gives it Dshot capability (click here)](../RM-XR2-PWM-Mod/readme.md).

I have [a few builds of AM32](builds) for a few ESCs that are popular in combat robotics (click on the link). The name of the files indicate what actual AM32 version the build is based on.

The source code for the code modification, is on a branch, of my fork, my fork of AM32. It is here: https://github.com/frank26080115/AM32/tree/fix-dshot-reliability-20250520

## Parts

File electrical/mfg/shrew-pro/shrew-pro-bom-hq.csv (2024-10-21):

Comment | Designator | Footprint | LCSC Part #
schottky 40V | D1 | SOD-323 | C151511
1n | C21 | 0402 | C307441
10uH | L1 | 0805 | C139245
10K | R1 R3 R4 | 0402
10nF | C19 C20 | 0402 | C3855387
10uF 50V | C2 C3 C4 C5 C6 C7 C8 C9 C10 C11 C15 | 0805 | C2932476
15uH | L2 | 0805 | C486333
X1G0054410320 | Y2 | OSC_TG2016SMN_50.0000M-ECGNNMB | C7503930
68K | R2 | 0402
100nF 50V | C1 C12 C13 C14 C22 C23 C24 C26 C27 C28 C29 C30 | 0402-CAP | C527001
0.5pF 50V | C31 | 0402-CAP | C258483
470nF | C16 C18 C25 | 0402 | C106250
2450FM07D0034001T | Y1 | FIL_2450FM07D0034T | C2651081
ANT3216LL00R2400A | ANT1 ANT2 | ANTENNA-CHIP2 | C293767
DRV8244HQRYJRQ1 | U3 U4 | RYJ0016A-MFG | C5699906
ESP32-PICO-D4 | U1 | PQFN50P700X700X104-49N | C193707
LMR16006YQ3DDCTQ1 | IC1 | SOT95P280X110-6N | C2071392
SK6812-EC20 | LED1 | SK6812-EC20 | C2909058
SX1280IMLTRT | U2 | QFN24_4X4_SEM | C125969

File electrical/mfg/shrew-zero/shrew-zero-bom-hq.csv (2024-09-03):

Comment | Designator | Footprint | LCSC Part #
schottky 40V | D1 | SOD-323 | C151511
0p5 | C28 | 0402-REV | C258483
1n | C20 | 0402-REV | C307441
10uH | L1 | 0805 | C139245
10K | R1 R3 R4 | 0402-REV
10n | C18 C19 | 0402-REV | C3855387
10u | C2 C3 C4 C5 C6 C7 C8 C9 C10 C14 | 0805 | C2932476
15u | L2 | 0805 | C486333
52MHz TCXO | Y2 | OSC_TG2016SMN_50.0000M-ECGNNMB | C7503930
68K | R2 | 0402-REV
100n | C1 C11 C12 C13 C21 C22 C23 C27 | 0402-REV | C527001
470n | C15 C17 C24 C25 C26 | 0402-REV | C106250
2450FM07D0034001T | Y1 | FIL_2450FM07D0034T | C2651081
ANT3216LL00R2400A | ANT1 ANT2 | ANTENNA-CHIP2 | C293767
ESP32-PICO-D4 | U1 | PQFN50P700X700X104-49N | C193707
LMR16006YQ3DDCTQ1 | IC1 | SOT95P280X110-6N | C2071392
SK6812-EC20 | LED1 | SK6812-EC20 | C2909058
SX1280IMLTRT | U2 | QFN24_4X4_SEM | C125969

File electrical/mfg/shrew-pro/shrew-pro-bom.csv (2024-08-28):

Comment | Designator | Footprint | LCSC Part #
schottky 40V | D1 | SOD-323 | C151511
1n | C21 | 0402
10uH | L1 | 0805 | C139245
10K | R1 R3 R4 | 0402
10nF | C19 C20 | 0402
10uF 50V | C2 C3 C4 C5 C6 C7 C8 C9 C10 C11 C15 | 0805 | C2932476
15uH | L2 | 0805 | C486333
X1G0054410320 | Y2 | OSC_TG2016SMN_50.0000M-ECGNNMB | C7503930
68K | R2 | 0402
100nF 50V | C1 C12 C13 C14 C22 C23 C24 C26 C27 | 0402-CAP | C1581
470nF | C16 C18 C25 | 0402
2450FM07D0034001T | Y1 | FIL_2450FM07D0034T | C6054595
74889302450 | ANT1 ANT2 | ANTENNA-CHIP2 | C6828492
DRV8244HQRYJRQ1 | U3 U4 | RYJ0016A-MFG | C5699906
ESP32-PICO-D4 | U1 | PQFN50P700X700X104-49N | C193707
LMR16006YQ3DDCTQ1 | IC1 | SOT95P280X110-6N | C2071392
SK6812-EC20 | LED1 | SK6812-EC20 | C2909058
SX1280IMLTRT | U2 | QFN24_4X4_SEM | C125969

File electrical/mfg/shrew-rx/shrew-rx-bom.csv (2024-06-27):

Comment | Designator | Footprint | LCSC Part #
1n 50V | C1 | 0402-CAP
BZT52C3V6S-7-F | D1 | SOD-323
10K 1% | R1 R2 R3 | 0402-RES
10n 50V | C3 C4 | 0402-CAP
10uF 25V | C11 | 0805
15u | L1 | 0805
X1G0054410320 | Y1 | OSC_TG2016SMN_50.0000M-ECGNNMB
100n 16V | C5 C6 C7 C8 C9 C10 | 0402-CAP
470n 16V | C2 C13 C17 | 0402-CAP
2450FM07D0034001T | FL1 | FIL_2450FM07D0034T
ESP32-PICO-D4 | U1 | PQFN50P700X700X104-49N
SK6812-EC20 | LED1 | SK6812-EC20
SX1280IMLTRT | U2 | QFN24_4X4_SEM
74889302450 | ANT1 ANT2 | ANTENNA-CHIP2

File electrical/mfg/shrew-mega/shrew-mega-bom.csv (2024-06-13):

Comment | Designator | Footprint
100nF 50V | C9 | 0402-CAP
100nF 50V | C10 | 0402-CAP
62K | R1 | 0402-RES
10uF 50V | C1 | 0805
10uF 50V | C2 | 0805
10uF 50V | C3 | 0805
10uF 50V | C4 | 0805
10uF 50V | C5 | 0805
10uF 50V | C6 | 0805
10uF 50V | C7 | 0805
10uF 50V | C8 | 0805
MIC5239-3.3YS-TR | IC1 | SOT223
DRV8244HQRYJRQ1 | U1 U2 | QFN

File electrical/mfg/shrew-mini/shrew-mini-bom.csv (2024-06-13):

Comment | Designator | Footprint | LCSC Part #
100nF 50V | C6 | 0402-CAP
100nF 50V | C7 | 0402-CAP
62K | R1 | 0402-RES
10uF 50V | C1 | 0805
10uF 50V | C2 | 0805
10uF 50V | C3 | 0805
10uF 50V | C4 | 0805
10uF 50V | C5 | 0805
DRV8231ADSGR | U1 U2 | WSON8
DS8242-33A3L | IC1 | SOT89

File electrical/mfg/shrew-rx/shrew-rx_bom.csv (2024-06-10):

Comment | Designator | Footprint | LCSC Part #
1n | C1 | 0402-CAP
3V6 | D1 | SOD-323
10K | R1 R2 R3 | 0402-RES
10n | C3 C4 | 0402-CAP
10uF 25V | C11 | 0805
15u | L1 | 0805
52MHz TCXO | Y1 | OSC_TG2016SMN_50.0000M-ECGNNMB
100n | C5 C6 C7 C8 C9 C10 | 0402-CAP
470n | C2 C13 C17 | 0402-CAP
2450FM07D0034T | FL1 | FIL_2450FM07D0034T
74889302450 | ANT1 ANT2 | ANTENNA-CHIP2
ESP32-PICO-D4 | U1 | PQFN50P700X700X104-49N
SK6812-EC20 | LED1 | SK6812-EC20
SX1280IMLTRT | U2 | QFN24_4X4_SEM

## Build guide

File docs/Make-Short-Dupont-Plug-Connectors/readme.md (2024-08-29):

If you think standard servo plugs are a bit too long, I have a simple and easy technique for making much shorter dupont female connectors.

Have a look at the original servo connector, the internal crimp of the servo connector, and compare that against the length of the standard male header pin.

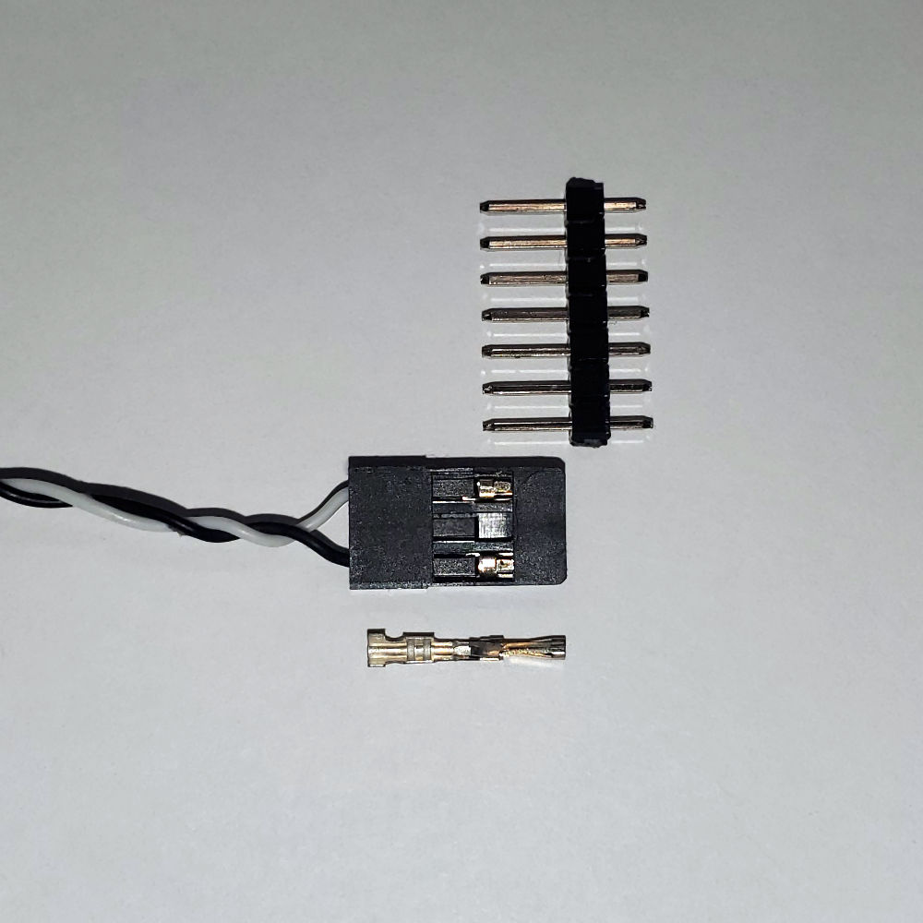
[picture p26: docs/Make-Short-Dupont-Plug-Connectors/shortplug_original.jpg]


The servo connector is clearly twice as long as the male header pins.

Making the shorter version is easy. Simply cut the crimp to be the same length as the male pin, discard the tail. Then solder the wire to the back side of the crimp.

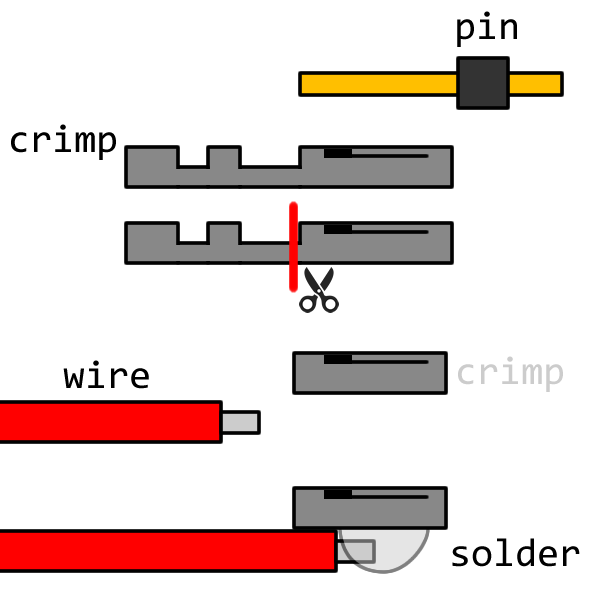
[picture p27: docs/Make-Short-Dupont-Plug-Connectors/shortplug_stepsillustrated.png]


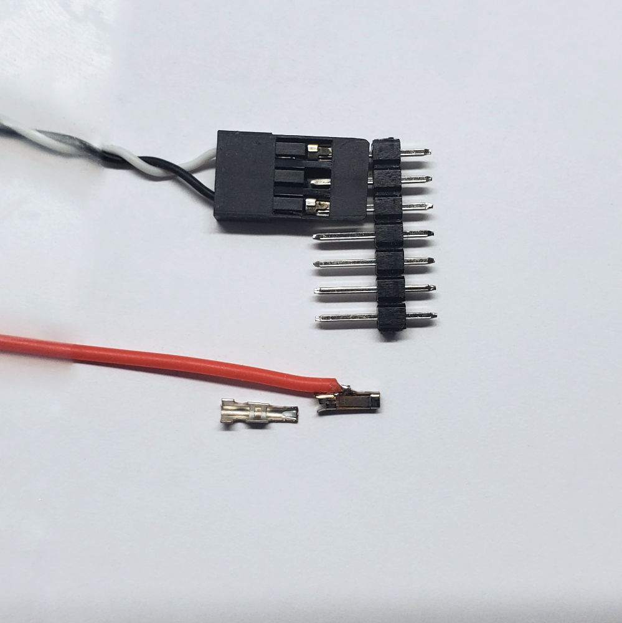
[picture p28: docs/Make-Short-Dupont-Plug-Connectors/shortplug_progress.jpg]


When soldering, make sure you don't get any solder inside of the crimp, do not let the solder leak into the seams.

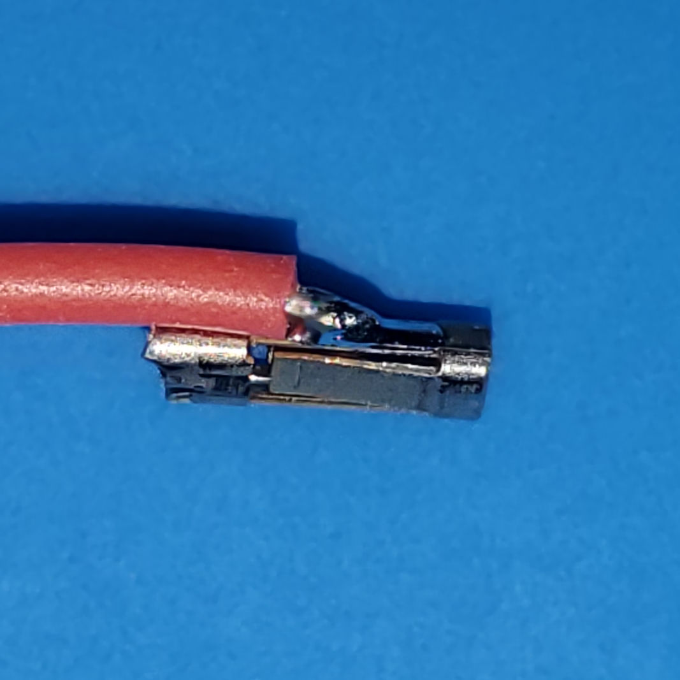
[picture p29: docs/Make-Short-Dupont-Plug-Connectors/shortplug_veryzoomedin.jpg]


Use a small bit of heat-shrink tubing to protect the wire and the crimp.

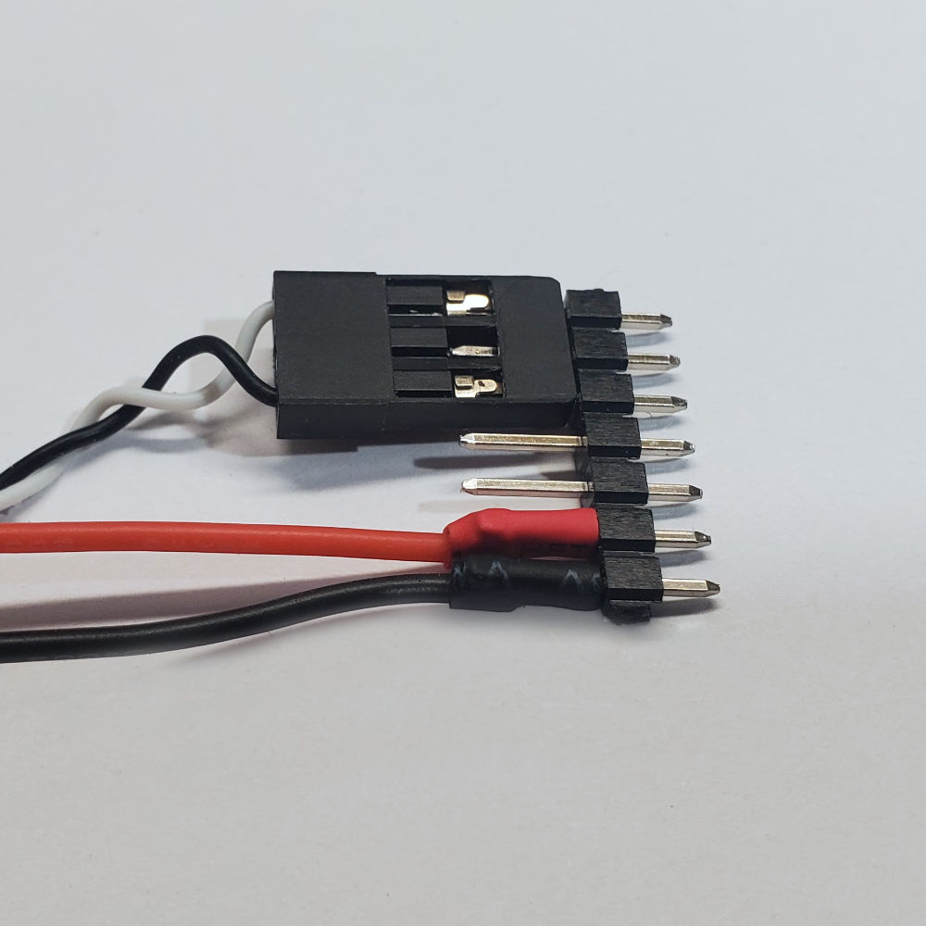
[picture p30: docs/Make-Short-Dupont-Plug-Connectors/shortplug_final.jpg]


You are finished.

I recommend using 28AWG wire for this, or even 30AWG wire, as long as the wire is stranded-core. Also, using silicone jacketed wire will make this much easier.

(only use thin wires for signalling wires, not power wires, power wires need to be appropriately thick)

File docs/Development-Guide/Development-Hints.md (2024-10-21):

# Shrew Firmware Development Hints

## Summary of Project Structure

The ExpressLRS firmware is written as a PlatformIO project. The programming language is C++ mostly. It supports multiple microcontroller architectures but all of the code is built on top of the Arduino framework. Shrew is built with a ESP32 microcontroller.

Every firmware build comprises of two parts: the firmware binary itself, and a block of default configuration data. The block of configuration data is what contains the pin mappings. The configuration can be changed later through the Wi-Fi web interface.

The flash memory comprises of 3 parts: the firmware, the EEPROM (it's an emulated EEPROM), and the file-system. There are some rules about firmware updating that determines if the EEPROM and file-system is erased during the update. Sometimes they are erased, sometimes they are not. If you need to, PlatformIO provides a specific button to erase all of the flash memory. During development and testing, I recommend you always erase flash memory completely.

The firmware is multitasking, but it is not using RTOS threads. FreeRTOS is available in the project for Shrew as it is using ESP32, but multithreading is not heavily used.

The firmware has some core functionality, which handles how the transmitter and receiver communicates. The other functions are implemented as "Devices", which are individual state machines.

The build process is taken care of by PlatformIO but there are some Python scripts that are used to pack all the HTML files and JSON files into the firmware.

NOTE: web pages being served by the Wi-Fi mode are not stored in file-system, they are actually compiled into the code with the help of some python scripting

## Cardinal Rules

Do not use the multithreading features of FreeRTOS. The ESP32 has two cores, and the firmware has already been written in a way that assigns tasks to each of the cores. Adding more threads will cause more unpredictable execution order.

Do not let your code run in a long loop that blocks other code from running. Do not use delays. Basically: do not write code that can cause the radio to miss a packet!

Do not halt the timers that the core code depends on. Do not disable any interrupts.

All of the above pretty much means: please use state machines

Do not use pins that are forbidden to be used on the ESP32 (there are some internal memory pins that cannot be used).

## How to Change Pin Assignments

Please also see the page on [Reassigning Pins](../Reassigning-Pins.md), which shows some of the pins that can be reassigned and also extra pins such as a +3.3V power supply pin.

The majority of pin assignments are defined in a set of JSON files under the `ExpressLRS/src/hardware/RX` directory.

For Shrew, the two files are `ShrewESC.json` and `Shrew-Zero.json` depending on which variation of Shrew you want to use.

For all other ExpressLRS hardware, you need to read through `targets.json` under the directory `ExpressLRS/src/hardware` to figure out which file should be edited.

For Shrew-Lite and Shrew-Pro (which uses the term `ShrewESC` in the code), the pin assignments for the H-bridge inputs are hard-coded in the source code, not in the JSON files. These pins are `GPIO9`, `GPIO10`, `GPIO13`, and `GPIO27`.

**IMPORTANT**: If you are using pins for purposes other than PWM output, please remember to remove them from the list of PWM pins!!! You can do this through editing these JSON files. You might need to also remove it as the RX and TX pin.

## How to Set Default User Options

Look inside the `ExpressLRS/src` directory for a file named `user_defines.txt`. Edit this file as you wish before compiling.

This can be useful for testing as it allows you to preset the binding phrase and lower the time before enabling Wi-Fi.

## How to Set Compiler Flags

Look inside the `ExpressLRS/src/targets` directory for a file named `shrew.ini`. It would also be helpful if you read `unified.ini` as well. You will see how the build flags are defined and how they are inherited.

If you do edit `shrew.ini` or `unified.ini`, PlatformIO will not detect the change immediately. But look inside the directory `ExpressLRS/src` for `platformio.ini`. Make a small change, like add a spacebar, revert the change, and then save it. Changes to `platformio.ini` will force PlatformIO to refresh all build options.

## Adding Code

If you are new at adding code to ExpressLRS, then I suggest you add it to an existing file. Look inside the directory `ExpressLRS/src/lib`, which will have a list of subdirectories with small code modules. Find the one that is related to what you want to add.

As an example, Shrew's ability to control H-bridge drivers is similar to outputting PWM pulses for servos. So I added the code into the `ServoOutput` module.

The neat thing about the `ServoOutput` module is that it contains code that is constantly running.

## Adding Web Pages

Web pages and other files that needs to be served are stored in the `ExpressLRS/src/html` directory. They are not automatically included. You need to also:

 * edit `ExpressLRS/src/lib/WIFI/devWIFI.cpp`, look for a variable called `files[]`, and add your file to the list
 * edit `ExpressLRS/src/python/build_html.py`, look for a function named `build_common`, and add your file to the list, make sure the parameters match the parameters from the previous step

The files can have pre-processor actions. I suggest you read the existing files to see how those are used. The pre-processor directives use the `@@` symbol.

NOTE: whitespace is stripped from HTML files to save space, which might break JavaScript placed in HTML files

NOTE: the files are minified and gzip compressed automatically, so don't worry too much about saving memory

If you need additional backend handling of HTTP requests, you will need to add handlers to the actual source code. The file you are interested in is `ExpressLRS/src/lib/WIFI/devWIFI.cpp`. The firmware uses the `ESPAsyncWebServer` library extensively. If you know how to use this library then you will have the skills to add backend functionality, it's documentation is here: https://github.com/me-no-dev/ESPAsyncWebServer

If you do not want to add code to `devWIFI.cpp` itself, then write functions that can take the `server` object as a parameter and add the handlers to that object.

## Adding a LED Strip

Open `ShrewESC.json` or `Shrew-Zero.json`, depending on which one you want to use, look for the block of code that looks like

    "led_rgb": 5,
    "led_rgb_isgrb": true,
    "ledidx_rgb_status": [0],
    "ledidx_rgb_boot": [0],

`led_rgb` is the pin number, change it however you need to. Remember to remove it from other functions, such as PWM.

To make the LED strip 8 LEDs long, then make the block look like

    "led_rgb": 5,
    "led_rgb_isgrb": true,
    "ledidx_rgb_status": [0, 1, 2, 3, 4, 5, 6, 7],
    "ledidx_rgb_boot": [0, 1, 2, 3, 4, 5, 6, 7],

## Debug Logging

If you edit `user_defines.txt` and uncomment the flag `-DDEBUG_LOG`, then the UART serial port will output all the printable items that are in the code using functions such as `DBG()` and `DBGLN()`, see the file `logging.h` for a list of available debug message functions (and read the source code to see examples of how they are used).

To view the messages, you will need to open the serial port using some sort of terminal software, with the baud rate 115200. I think you can use the `monitor` option of PlatformIO. There are also a few Visual Studio Code extensions that are serial terminals.

## Git Repo Branches

The branch `shrew-dev` is the actively work-in-progress branch. The code is not considered released and is likely not bug-free.

The branch `shrew` is a release branch. All the firmware being distributed or preloaded will come from this branch.

Once in a while, you probably want to update your own branch to be in-sync with my `shrew` branch. To do so:

 1. make a temporary branch: `git checkout -b temp-branch upstream/shrew`
 2. go back to your own branch: `git checkout your-branch-name`
 3. perform merge: `git merge temp-branch`
 4. resolve any merge conflicts
 5. delete temporary branch: `git branch -d temp-branch`

To sync with a particular version tag, go through these steps (example uses the tag `3.5.0` from the parent ExpressLRS repo):

 1. update local tags metadata: `git fetch upstream --tags`
 2. make a temporary branch: `git checkout -b temp-branch 3.5.0`
 3. go back to your own branch: `git checkout your-branch-name`
 4. perform merge: `git merge temp-branch`
 5. resolve any merge conflicts
 6. delete temporary branch: `git branch -d temp-branch`

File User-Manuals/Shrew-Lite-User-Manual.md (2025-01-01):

# Shrew-Lite User Manual

Shrew-Lite is a dual brushed motor ESC with an integrated ExpressLRS RC radio receiver.

 * Maximum voltage: 33V
 * Recommended battery voltage: 6V-26V (2S-6S lithium ion)
 * Current rating per brushed motor channel: 3.7A each
 * See this document: [Motor Driver Specs](docs/Motor-Driver-Specs.md)
 * Has over-current protection and over-temperature protection
 * 4 digital outputs, capable of PWM, PWM-stretched, DShot, CRSF, SBUS

## Pin Map

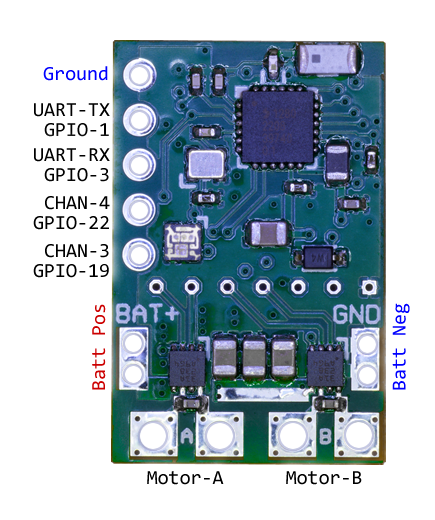
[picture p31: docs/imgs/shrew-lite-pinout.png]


Motor-A is assigned to channel 1. Motor-B is assigned to channel 2. These assignments cannot be changed.

The `CHAN` number is the PWM channel number under default configuration. The `GPIO` numbers are the ones that can be used in the JSON configuration or in the firmware source code. The `UART`, aka serial port, can be remapped. A second serial port can be configured by the user. Note that the UART pins can be used for additional PWM/DSHOT pins if you want 4 channels instead of 2 channels.

## Dimensions

24mm length by 15.5mm width

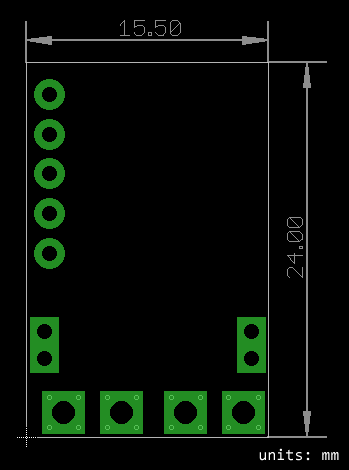
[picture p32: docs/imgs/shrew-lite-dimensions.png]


## LED Blink Meaning

| Behaviour | Meaning |
|---|---|
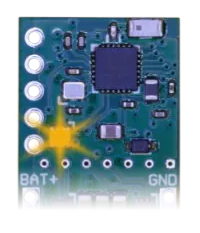
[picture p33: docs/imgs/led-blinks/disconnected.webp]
|  | not connected, waiting for connection <br> orange regular blink |
|  | not bound, please bind it to a transmitter <br> orange double blink |
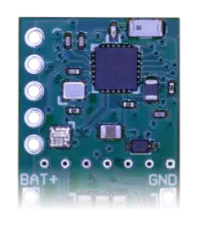
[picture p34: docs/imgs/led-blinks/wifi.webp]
|  | Wi-Fi mode <br> green yellow green animation |
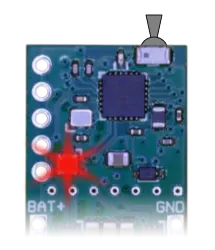
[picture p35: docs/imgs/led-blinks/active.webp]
|  | connected and active <br> solid colour, colour changes as the radio transmitter sticks/channels move |

(above table contains animations, appologies if they are not playing correctly)

## Transmitter Preperation

Just in case you need it, here are some links to official ExpressLRS instructions on how to prepare your transmitter:

 * [Radio Preperation](https://www.expresslrs.org/quick-start/transmitters/tx-prep/)
 * [Lua Script Install](https://www.expresslrs.org/quick-start/transmitters/lua-howto/)

**Important Note:** Your transmitter can run official ExpressLRS firmware, as long as it is version `3.3.0` and later. **You can use ExpressLRS Configurator to update your transmitter**

**Important Note Continued:** The Shrew firmware is not official ExpressLRS firmware, and does not have to match to the transmitter firmware. **Do not use the ExpressLRS Configurator to update Shrew**.

I hope you have followed the instructions above and have access to the ExpressLRS Lua script on your transmitter. Run the `ExpressLRS` script, scroll down and select `WiFi Connectivity`, and then select `Enable WiFi`.

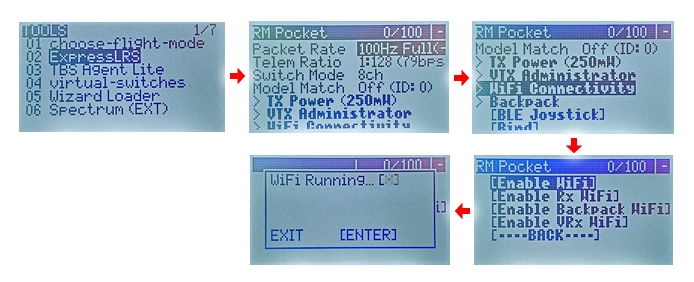
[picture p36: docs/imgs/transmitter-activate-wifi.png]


From your phone or computer, connect to the `ExpressLRS TX` Wi-Fi access point. The password is `expresslrs`.

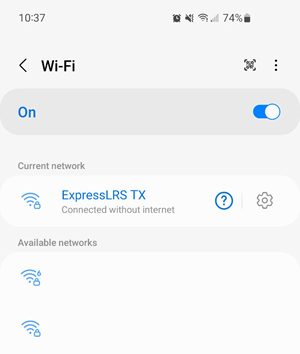
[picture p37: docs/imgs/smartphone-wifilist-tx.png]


Use your web-browser to navigate to `http://10.0.0.1/`

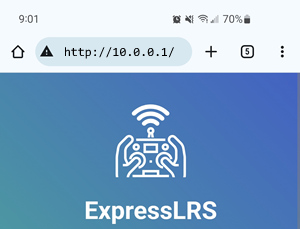
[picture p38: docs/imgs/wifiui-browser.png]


Scroll down and edit the binding-phrase and then save it.

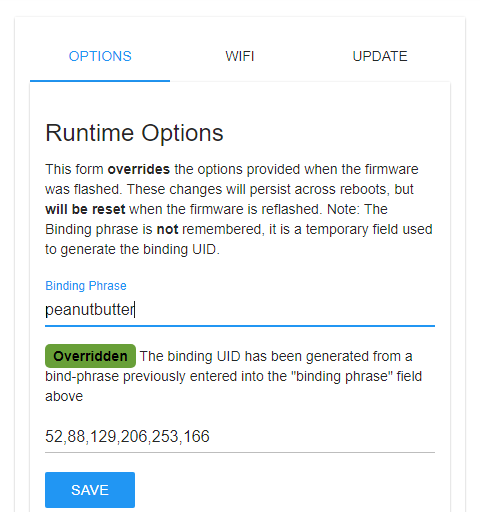
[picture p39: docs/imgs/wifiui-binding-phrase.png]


Once you have saved it, **turn off the radio**, or at least exit Wi-Fi mode.

## First Time Binding

Connect the Shrew to a power source. Shrew is designed to be directly connected to a battery, no pre-conditioning (such as a BEC) is required. The LED should start blinking orange. Wait for about 60 seconds. Then the LED will start to go crazy (it's like a green-yellow fading animation). This means the Shrew has activated its own Wi-Fi access point.

Using your phone or computer, connect to the `ExpressLRS RX` Wi-Fi access point. The password is `expresslrs`.

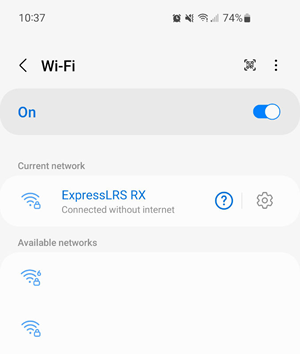
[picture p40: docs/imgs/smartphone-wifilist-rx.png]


Use your web-browser to navigate to `http://10.0.0.1/`



Scroll down and edit the binding-phrase and then save it.



Once you have done that, Shrew should be ready to use with default settings.

**IMPORTANT:** The Shrew firmware disables the activation of binding mode by power cycling it 3 times. This is done to prevent accidental activation of binding mode.

## Please Set Packet-Rate

ExpressLRS has a variety of packet rates to choose from. The higher packet rates are better for faster responses and reconnects faster, but sends less data, only four channels of data will have full resolution, and the other channels will have low resolution and worse response times. The lower data rates can send all channels at full resolution.

Use the `ExpressLRS` Lua script again, set the `Packet Rate` option to `1000Hz` if you want the fastest rate, or choose the slower `100Hz - Full` if you need all the channels to be full resolution

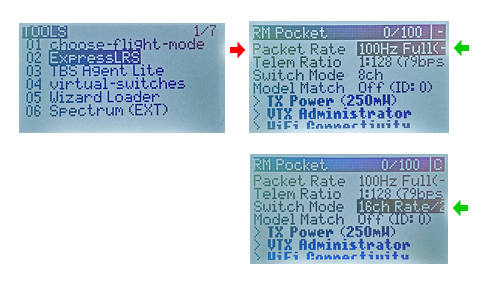
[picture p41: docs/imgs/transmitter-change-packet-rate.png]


For a full explanation, ExpressLRS officially has this documentation: https://www.expresslrs.org/software/switch-config/ .

If you want the best possible performance, read the section on `Packet Rate Lock` later on.

## First Test

Have your radio transmitter powered up and ready to use. Power-cycle Shrew, it should connect to your transmitter, the LED should stay a solid colour, and your transmitter should indicate that it is connected (you might see a RSSI symbol somewhere on your screen).



Moving any sticks/channels on the transmitter should make the LED on the Shrew change colour. (experimental feature, ExpressLRS receivers don't typically do this, but Shrew firmware does)

## Robot Drive Mixing

I have provided mixes for your transmitter. It involves copying a file to your transmitter's microSD card. Please see [this page for full details](tx-mixes/readme.md).

Otherwise, make your own mix however you want, just remember that Motor-A is always channel 1 and Motor-B is always channel 2.

## Activating Wi-Fi

To configure anything on Shrew, you need to connect to its web-ui via Wi-Fi. There are two ways of activating Wi-Fi on Shrew.

 * Powering it up without a transmitter, and then waiting for 60 seconds. (this time period is configurable)
 * Powering it up, connect it to the transmitter, and then using the transmitter's Lua script to activate Wi-Fi. This is similar to activating the transmitter's own Wi-Fi, but you use the `[Enable Rx WiFi]` option instead.

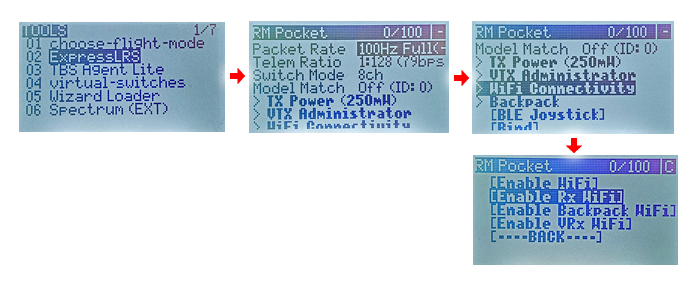
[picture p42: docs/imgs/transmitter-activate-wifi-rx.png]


From your phone or computer, connect to the `ExpressLRS TX` Wi-Fi access point. The password is `expresslrs`.



Use your web-browser to navigate to `http://10.0.0.1/`



## Editing the Channels

Once you are on the Wi-Fi web-ui page, you should see a table like this:

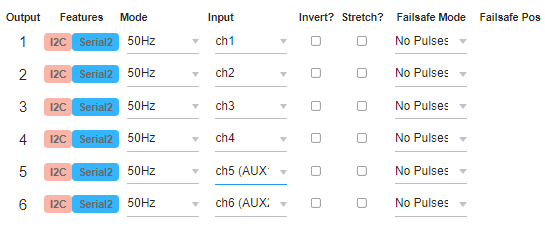
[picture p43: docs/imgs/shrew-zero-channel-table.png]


If you are using a ESC that supports DShot protocol (specifically DSHOT300), it is recommended that you change the `Mode` drop-down to `DShot`. Otherwise, use `50Hz` mode for servos and ESCs that do not support DShot. Ignore the other modes for now.

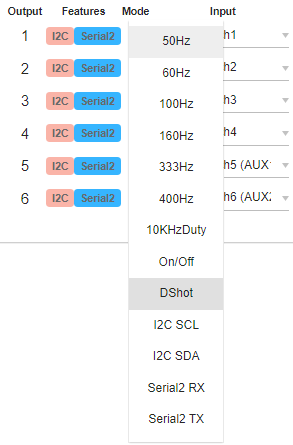
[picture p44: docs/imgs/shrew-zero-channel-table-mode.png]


To rearrange the channel mapping, use the `Input` drop-down to select the radio channel that the output should be mapped to.

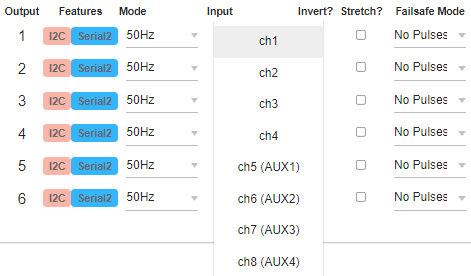
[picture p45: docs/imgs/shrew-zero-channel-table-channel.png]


The servo-stretching feature can be activated by checking the `Stretch?` checkbox. Servo stretching means that the sent PWM pulse width is from 476us to 2524us instead of 988us to 2012us. This is useful for wide range servos.

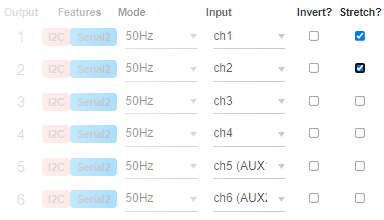
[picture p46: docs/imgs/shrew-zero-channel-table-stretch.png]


The failsafe mode should be left at `No Pulse`, this is the safest option. (other options are explained)

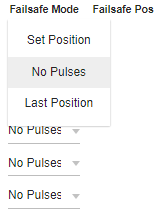
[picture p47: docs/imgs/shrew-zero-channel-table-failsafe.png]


## Other Notable Options

#### Packet Rate Lock

I recommend you activate this option:

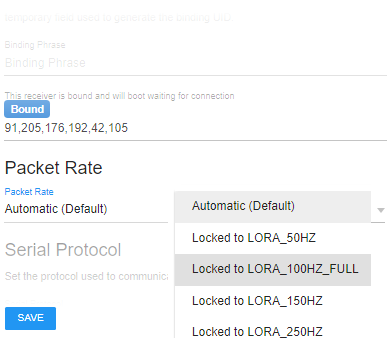
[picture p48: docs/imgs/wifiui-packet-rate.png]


In the previous steps, I have asked you to set the packet-rate to 1000Hz or 100Hz already. Locking it on Shrew will allow for it to reconnect a bit faster when power is lost. However, while locked, the Lua script will not be able to edit the packet-rate anymore.

#### AM32 Configurator

While connected to the Wi-Fi web-ui, use the web browser to visit `http://10.0.0.1/am32.html`

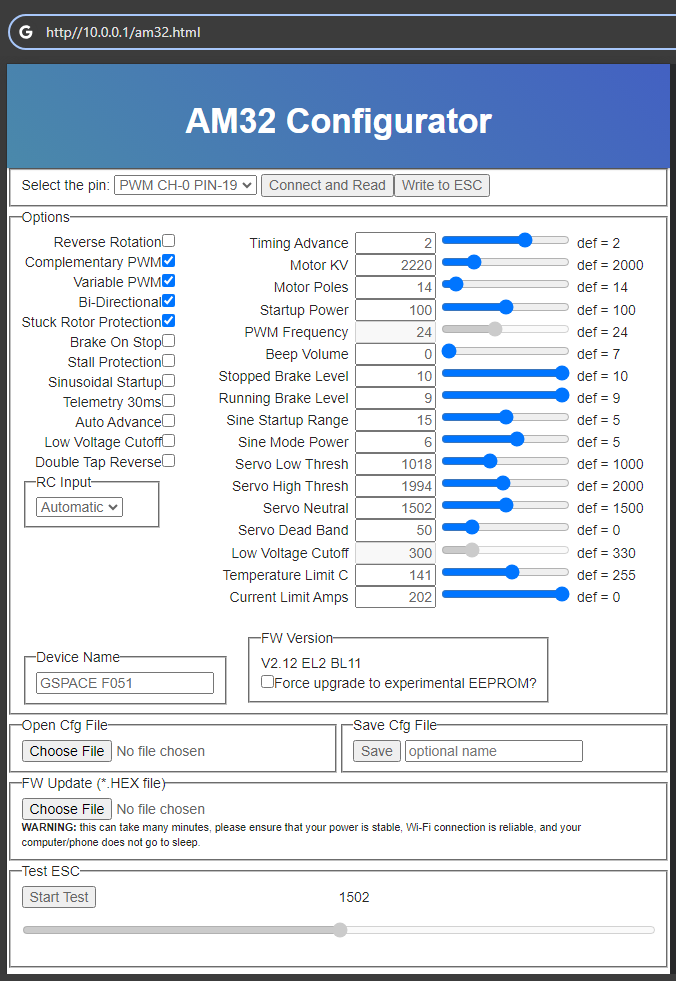
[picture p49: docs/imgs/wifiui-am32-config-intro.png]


#### More Advanced Usage

ExpressLRS is open source, and the source code for Shrew is a fork of the ExpressLRS source code. If you wish to add your own features to Shrew's source code, the starting point is at [https://github.com/frank26080115/ExpressLRS/tree/shrew](https://github.com/frank26080115/ExpressLRS/tree/shrew).

The GPIOs are capable of things like I2C, an extra serial port, or even CAN bus.

## Firmware Update

If there is a firmware update, it will be provided from me personally, as you have a special prototype. Once you have the file, it can be uploaded to the `Update` tab in the Wi-Fi web-ui.

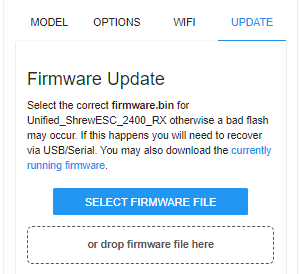
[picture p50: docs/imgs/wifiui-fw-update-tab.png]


**IMPORTANT:** Updating the firmware in any way will reset all settings to the default as specified in the firmware. Please double check your settings after every firmware update.

If you need to update the firmware via a USB-to-serial converter, then follow the instructions on [firmware updating via USB](docs/Firmware-Updating-via-USB.md). (for example, if Wi-Fi is unavailable due to corrupted firmware, or, if you are building the circuit at home instead of purchasing one)

## Wiring Hints

The design allows you to run the wires in one direction and then wrap it all in heat shrink tubing.

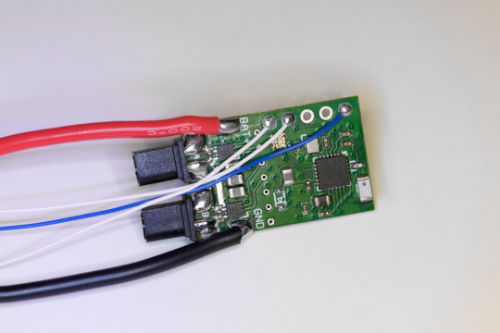
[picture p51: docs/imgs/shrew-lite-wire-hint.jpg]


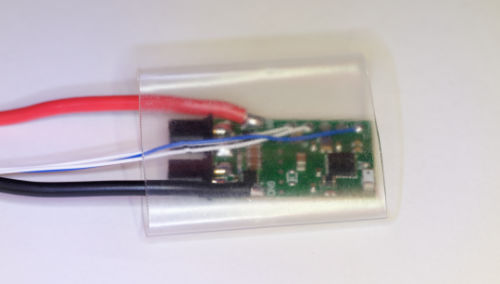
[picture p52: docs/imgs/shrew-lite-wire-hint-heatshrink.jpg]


The connectors I put on for the motors are GNB A30 connectors.

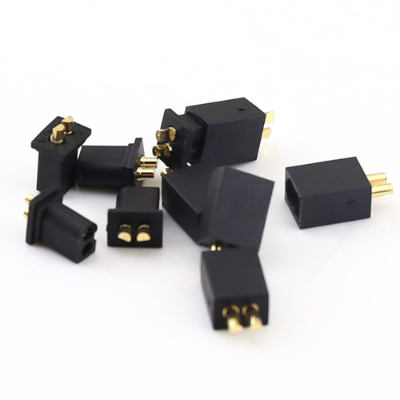
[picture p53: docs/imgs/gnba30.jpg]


Notice that I do not put the wires through the holes, the wires are soldered to the surface instead, there is enough solder to actually fill the holes though. This is all intentional and the way I recommend you solder wires to Shrew.

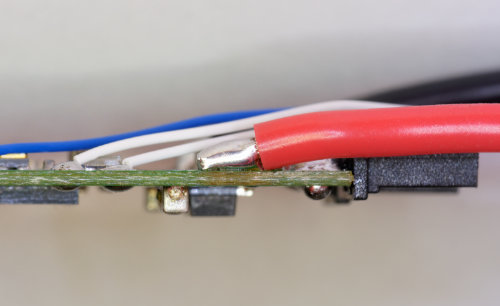
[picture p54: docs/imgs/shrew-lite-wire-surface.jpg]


## Appendix

 * [Reassigning Pins](docs/Reassigning-Pins.md)
 * [Digital Protocols for ESC Control](docs/Digital-Protocols-for-ESC-Control.md), and why they are better
 * [No-Pulse Failsafe Mode](docs/No-Pulse-Failsafe-Mode.md), and why it's safer

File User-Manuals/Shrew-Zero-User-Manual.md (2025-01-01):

# Shrew-Zero User Manual

Shrew-Zero is a ExpressLRS RC radio receiver with 8 signal output, and a power input rated for 40V.

 * all outputs support multiple protocols: PWM (default), DSHOT300, PWM-stretched
 * all channels feature no-pulse failsafe set by default
 * serial port transmits CRSF protocol packets by default
 * all outputs can be used to configure and test AM32 brushless ESCs
 * power input is rated for 40V continuous operation, up to 60V voltage spikes

## Pin Map

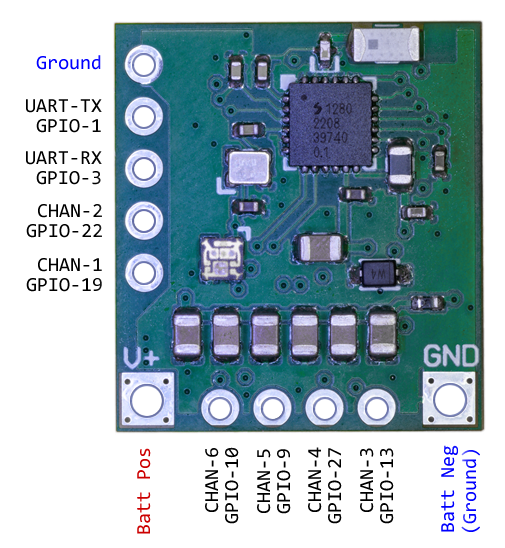
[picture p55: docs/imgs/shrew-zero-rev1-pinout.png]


The `CHAN` number is the PWM channel number under default configuration. The `GPIO` numbers are the ones that can be used in the JSON configuration or in the firmware source code. The `UART`, aka serial port, can be remapped. A second serial port can be configured by the user. Note that the UART pins can be used for additional PWM/DSHOT pins if you want 8 channels instead of 6 channels.

## Dimensions

20mm x 18mm

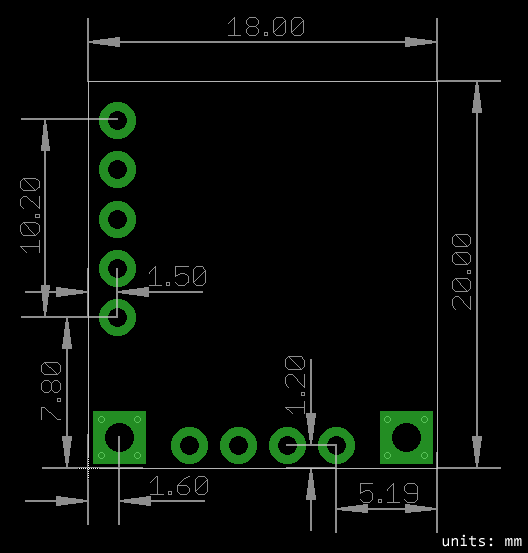
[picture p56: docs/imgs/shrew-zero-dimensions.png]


## LED Blink Meaning

| Behaviour | Meaning |
|---|---|
|  | not connected, waiting for connection <br> orange regular blink |
|  | not bound, please bind it to a transmitter <br> orange double blink |
|  | Wi-Fi mode <br> green yellow green animation |
|  | connected and active <br> solid colour, colour changes as the radio transmitter sticks/channels move |

(above table contains animations, appologies if they are not playing correctly)

## Transmitter Preperation

Just in case you need it, here are some links to official ExpressLRS instructions on how to prepare your transmitter:

 * [Radio Preperation](https://www.expresslrs.org/quick-start/transmitters/tx-prep/)
 * [Lua Script Install](https://www.expresslrs.org/quick-start/transmitters/lua-howto/)

**Important Note:** Your transmitter can run official ExpressLRS firmware, as long as it is version `3.3.0` and later. **You can use ExpressLRS Configurator to update your transmitter**

**Important Note Continued:** The Shrew firmware is not official ExpressLRS firmware, and does not have to match to the transmitter firmware. **Do not use the ExpressLRS Configurator to update Shrew-Zero**.

I hope you have followed the instructions above and have access to the ExpressLRS Lua script on your transmitter. Run the `ExpressLRS` script, scroll down and select `WiFi Connectivity`, and then select `Enable WiFi`.



From your phone or computer, connect to the `ExpressLRS TX` Wi-Fi access point. The password is `expresslrs`.



Use your web-browser to navigate to `http://10.0.0.1/`



Scroll down and edit the binding-phrase and then save it.



Once you have saved it, **turn off the radio**, or at least exit Wi-Fi mode.

## First Time Binding

Connect the Shrew to a power source. Shrew is designed to be directly connected to a battery, no pre-conditioning (such as a BEC) is required. The LED should start blinking orange. Wait for about 60 seconds. Then the LED will start to go crazy (it's like a green-yellow fading animation). This means the Shrew has activated its own Wi-Fi access point.

Using your phone or computer, connect to the `ExpressLRS RX` Wi-Fi access point. The password is `expresslrs`.



Use your web-browser to navigate to `http://10.0.0.1/`



Scroll down and edit the binding-phrase and then save it.



Once you have done that, Shrew should be ready to use with default settings.

**IMPORTANT:** The Shrew firmware disables the activation of binding mode by power cycling it 3 times. This is done to prevent accidental activation of binding mode.

## Please Set Packet-Rate

ExpressLRS has a variety of packet rates to choose from. The higher packet rates are better for faster responses and reconnects faster, but sends less data, only four channels of data will have full resolution, and the other channels will have low resolution and worse response times. The lower data rates can send all channels at full resolution.

Use the `ExpressLRS` Lua script again, set the `Packet Rate` option to `1000Hz` if you want the fastest rate, or choose the slower `100Hz - Full` if you need all the channels to be full resolution



For a full explanation, ExpressLRS officially has this documentation: https://www.expresslrs.org/software/switch-config/ .

If you want the best possible performance, read the section on `Packet Rate Lock` later on.

## First Test

Have your radio transmitter powered up and ready to use. Power-cycle Shrew-Zero, it should connect to your transmitter, the LED should stay a solid colour, and your transmitter should indicate that it is connected (you might see a RSSI symbol somewhere on your screen).



Moving any sticks/channels on the transmitter should make the LED on the Shrew change colour. (experimental feature, ExpressLRS receivers don't typically do this, but Shrew firmware does)

## Activating Wi-Fi

To configure anything on Shrew-Zero, you need to connect to its web-ui via Wi-Fi. There are two ways of activating Wi-Fi on Shrew-Zero.

 * Powering it up without a transmitter, and then waiting for 60 seconds. (this time period is configurable)
 * Powering it up, connect it to the transmitter, and then using the transmitter's Lua script to activate Wi-Fi. This is similar to activating the transmitter's own Wi-Fi, but you use the `[Enable Rx WiFi]` option instead.



From your phone or computer, connect to the `ExpressLRS TX` Wi-Fi access point. The password is `expresslrs`.



Use your web-browser to navigate to `http://10.0.0.1/`



## Editing the Channels

Once you are on the Wi-Fi web-ui page, you should see a table like this:



If you are using a ESC that supports DShot protocol (specifically DSHOT300), it is recommended that you change the `Mode` drop-down to `DShot`. Otherwise, use `50Hz` mode for servos and ESCs that do not support DShot. Ignore the other modes for now.



To rearrange the channel mapping, use the `Input` drop-down to select the radio channel that the output should be mapped to.



The servo-stretching feature can be activated by checking the `Stretch?` checkbox. Servo stretching means that the sent PWM pulse width is from 476us to 2524us instead of 988us to 2012us. This is useful for wide range servos.



The failsafe mode should be left at `No Pulse`, this is the safest option. (other options are explained)



## Other Notable Options

#### Packet Rate Lock

I recommend you activate this option:



In the previous steps, I have asked you to set the packet-rate to 1000Hz or 100Hz already. Locking it on Shrew will allow for it to reconnect a bit faster when power is lost. However, while locked, the Lua script will not be able to edit the packet-rate anymore.

#### AM32 Configurator

While connected to the Wi-Fi web-ui, use the web browser to visit `http://10.0.0.1/am32.html`



#### More Advanced Usage

ExpressLRS is open source, and the source code for Shrew is a fork of the ExpressLRS source code. If you wish to add your own features to Shrew's source code, the starting point is at [https://github.com/frank26080115/ExpressLRS/tree/shrew](https://github.com/frank26080115/ExpressLRS/tree/shrew).

The GPIOs are capable of things like I2C, an extra serial port, or even CAN bus.

## Firmware Update

If there is a firmware update, it must be obtained from [https://expresslrsconfig.eleccelerator.com/](https://expresslrsconfig.eleccelerator.com/), which is my firmware distribution mechanism for Shrew. **Official ExpressLRS firmware will not work for Shrew. Do not attempt to obtain a firmware using the official ExpressLRS GitHub repo or their configurator.**

Be sure to select `Shrew-Zero` as the receiver!

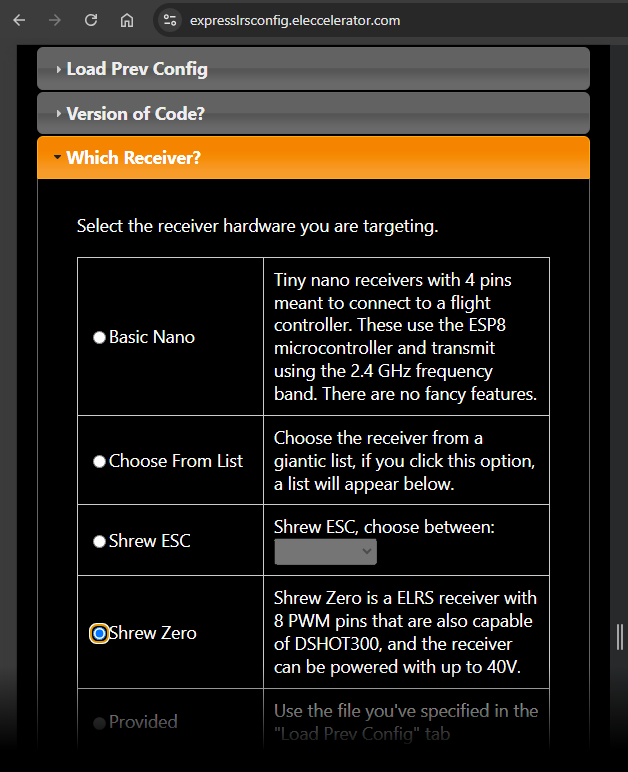
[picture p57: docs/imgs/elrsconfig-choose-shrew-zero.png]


Go ahead and configure the firmware however you like, just make sure the receiver is `Shrew Zero`. After you are ready, click on `Save for Wi-Fi Install`.

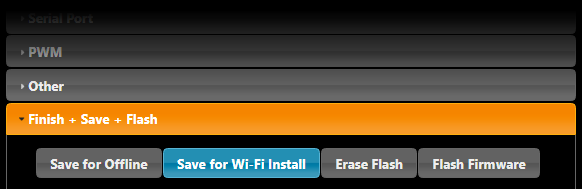
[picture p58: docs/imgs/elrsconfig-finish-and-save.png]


Once the firmware `*.bin` file has been downloaded, it can be uploaded to the `Update` tab in the Wi-Fi web-ui.



**IMPORTANT:** Updating the firmware in any way will reset all settings to the default as specified in the firmware. Please double check your settings after every firmware update.

If you need to update the firmware via a USB-to-serial converter, then follow the instructions on [firmware updating via USB](docs/Firmware-Updating-via-USB.md). (for example, if Wi-Fi is unavailable due to corrupted firmware, or, if you are building the circuit at home instead of purchasing one)

## Wiring Hints

Shrew-Zero is meant to allow the user total freedom in how they want to wire it. I expect most users to solder wires directly to it.

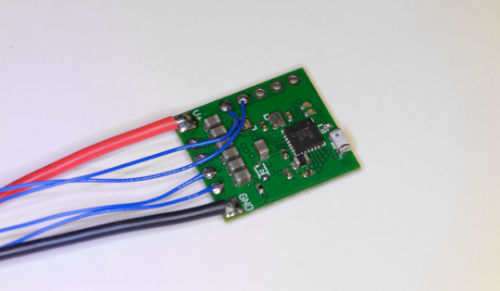
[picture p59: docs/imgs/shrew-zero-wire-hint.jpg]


The wires can be pretty thin, the signal wires require almost no current at all, the power wires need to handle 80mA normally, and 300mA at maximum.

If you want to add pins, here are some suggested ways:

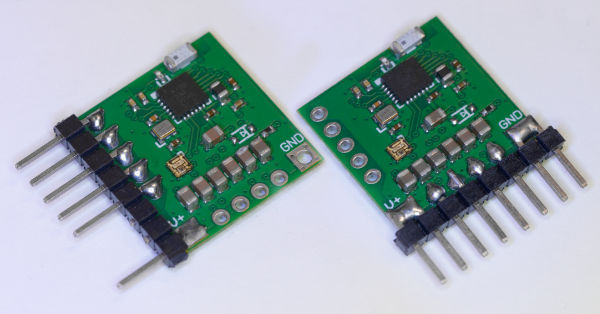
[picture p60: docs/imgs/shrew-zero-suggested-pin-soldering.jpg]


Notice that I did not use bent headers, I used straight headers, and the legs **did not** go into the holes. This is intentional and it is the way I am recommending you solder on pins. As long as you put enough solder to reach the other side of the board, joints like this is more than strong enough.

Recommended heat-shrink wrap size is 3/4"

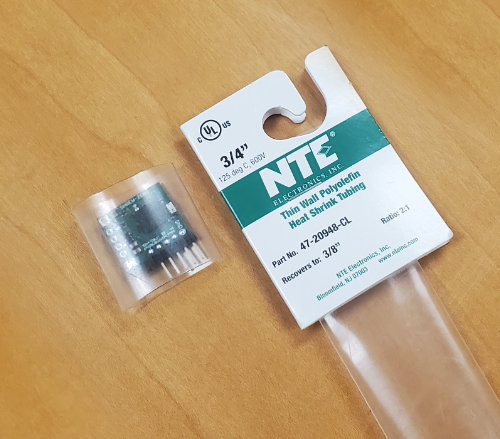
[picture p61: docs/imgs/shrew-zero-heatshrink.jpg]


If you want to learn how to make super short connectors, [check out this guide](docs/Make-Short-Dupont-Plug-Connectors/readme.md)

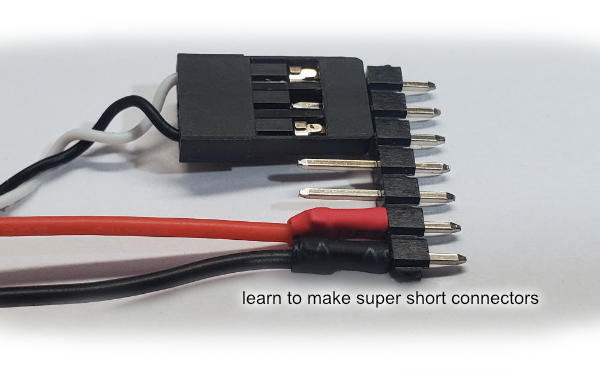
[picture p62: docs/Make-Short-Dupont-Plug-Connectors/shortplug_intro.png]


## Appendix

 * [Reassigning Pins](docs/Reassigning-Pins.md)
 * [Digital Protocols for ESC Control](docs/Digital-Protocols-for-ESC-Control.md), and why they are better
 * [No-Pulse Failsafe Mode](docs/No-Pulse-Failsafe-Mode.md), and why it's safer

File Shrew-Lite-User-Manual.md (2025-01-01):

[this document has been moved, please click here](User-Manuals/Shrew-Lite-User-Manual.md)

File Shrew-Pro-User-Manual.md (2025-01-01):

[this document has been moved, please click here](User-Manuals/Shrew-Pro-User-Manual.md)

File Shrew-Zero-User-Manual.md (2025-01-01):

[this document has been moved, please click here](User-Manuals/Shrew-Zero-User-Manual.md)

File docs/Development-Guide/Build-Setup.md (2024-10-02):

# Shrew Firmware Build Setup

To start developing customized firmwares for Shrew, you need to have the build tools used by the ExpressLRS project first, then obtain a copy of the Shrew firmware fork of the ExpressLRS firmware project.

ExpressLRS firmware is built using Visual Studio Code and PlatformIO (which uses the official ESP32 toolchain and Espressif Arduino framework internally)

## 1. Install Visual Studio Code

Go to https://code.visualstudio.com/ to download Visual Studio Code. Then install it.

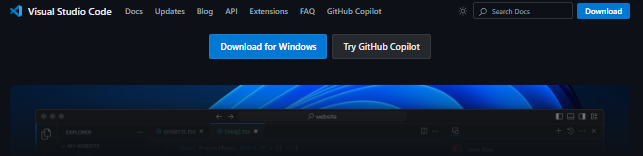
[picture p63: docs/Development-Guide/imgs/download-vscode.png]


## 2. Install PlatformIO

Open Visual Studio Code. On the side tool-bar, open the extensions manager. Use the search box to search for `PlatformIO IDE` and then install it.

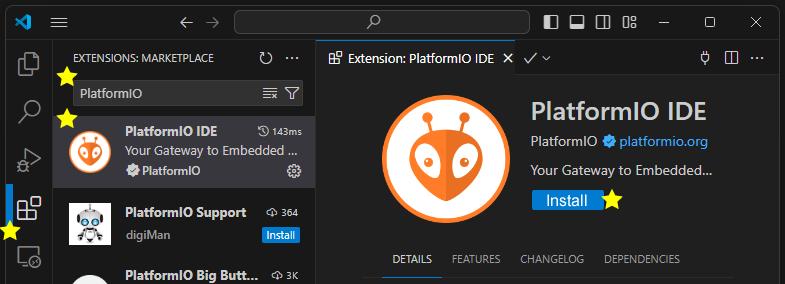
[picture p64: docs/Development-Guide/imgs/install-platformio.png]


Alternatively, there is also instructions on how to install PlatformIO on the PlatformIO website: https://platformio.org/install/ide?install=vscode

## 3. Setup GitHub

If you don't have a GitHub account, you should make a GitHub account. Log into your GitHub account.

Visit https://github.com/frank26080115/ExpressLRS/ (the most important thing here is that it's the fork of ExpressLRS but from my account, frank26080115's account)

Click on the `fork` button to make a fork into your own account.

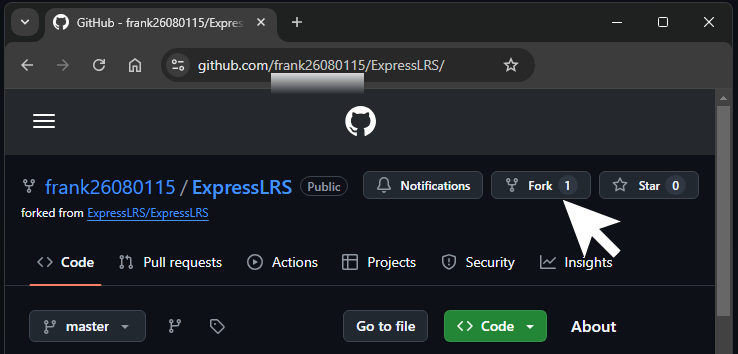
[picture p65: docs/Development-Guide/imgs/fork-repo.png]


If do not understand how to use Git, then I recommend you install GitHub Desktop first: https://desktop.github.com/download/

Once you have git or GitHub Desktop installed, visit your own fork of the repository, and then make a clone of it on your computer.



For the sake of an example, pretend you have cloned the repo into `C:\ExpressLRS`

## 4. Opening the Right Branch

Using GitHub Desktop, select the `ExpressLRS` repository, and then use the branch selector, select the `shrew` branch.



If the `shrew` branch is somehow not available, it means you did not perform the fork from the proper git repository, or you have multiple `ExpressLRS` projects and picked the wrong one with GitHub Desktop.

## 5. Opening the Project

Run Visual Studio Code. Use the menu to `open folder`. You need to open the `C:\ExpressLRS\src` directory.





## 6. Perform a Build

In the Visual Studio Code window, look on the side tool-bar, click on the PlatformIO icon



Expand the task that starts with `Unified_Shrew` and ends in `_UART`



This might take a while if this is a new PlatformIO installation, it will install the required tools to perform the build. After that you should see an option to do builds and uploads.

(if the `Unified_Shrew` option does not exist in the list of tasks, it means you are not using the right branch)





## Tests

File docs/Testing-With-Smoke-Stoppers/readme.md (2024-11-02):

# Testing With Smoke Stoppers

In the RC hobby (drones, robotics, etc), a "smoke stopper" is basically a fuse. It is inserted between a power source (battery) and the circuit being tested. If the circuit has a problem that causes an unusually large electrical current draw, the fuse will "blow", disconnecting the power, and hopefully preventing "smoke" (damage to circuit or power source).

This article will discuss using these smoke stoppers in the combat robotics hobby. It is my personal opinion that they are an essential tool for combat robotics competitors. I use one all the time. Every single time after I work on my robot's circuit, or after every robot fight, I use a smoke stopper during the next power-on test.

For example, it would've prevented this kind of accident:

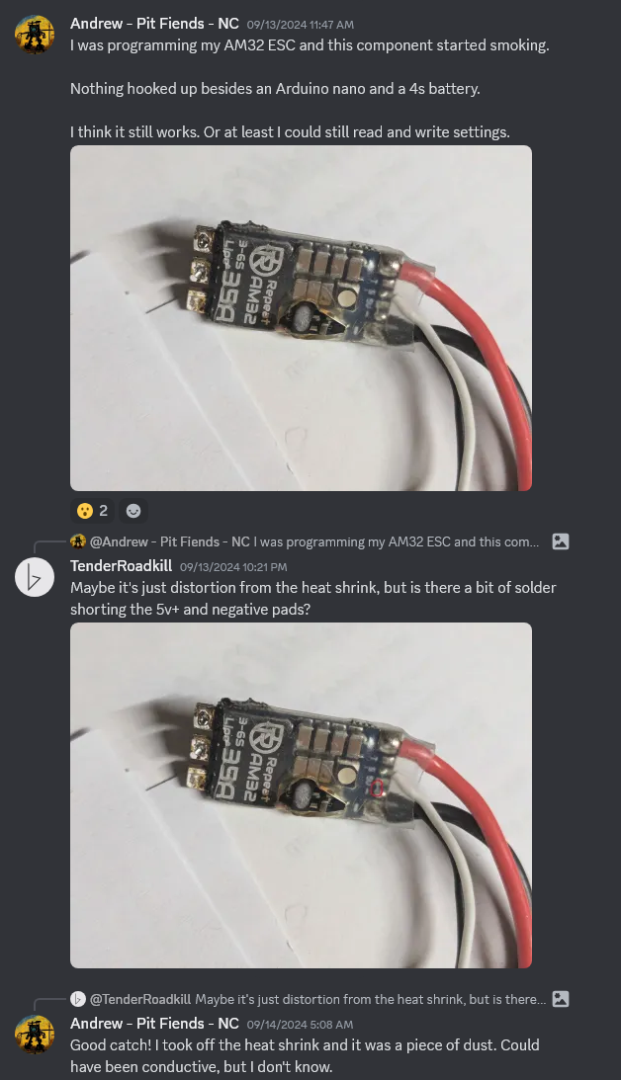
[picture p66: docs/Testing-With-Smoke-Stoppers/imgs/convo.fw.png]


# What Kind of Protection

These smoke stoppers typically only protect against unexpectedly high electrical current. They do NOT protect against high voltages. They also do NOT protect against reverse polarity.

Most importantly, they will prevent a battery from exploding from unexpectedly high discharge currents. They can prevent voltage conversion circuitry (voltage regulators and such) from being damaged from high currents. They can prevent MOSFETs from being damaged from high currents.

But again, I need to emphasize: they cannot prevent damage from high voltages or from reversed polarity.

If you do end up plugging in a battery backwards, or somehow connected a red wire to black wire, it is still likely that it results in a high current and the smoke stopper will trip, but it is not guaranteed. For example, a polarized capacitor in your circuit can still "pop" from such a mistake. But the important thing is that the battery will not explode if you make this mistake.
 
# What Kind of Smoke Stopper

There is literally only one smoke stopper that I can recommend: the ViFly Short Saver 2 Smoke Stopper

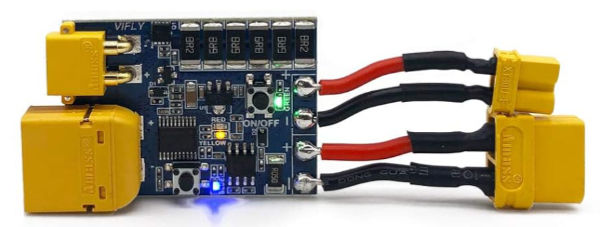
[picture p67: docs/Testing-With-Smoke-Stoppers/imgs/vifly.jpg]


 * [Repeat Robotics Store](https://repeat-robotics.com/buy/vifly-shortsaver-v2-smart-smoke-stopper/)
 * [Amazon Link](https://www.amazon.com/VIFLY-ShortSaver-Electronic-Short-Circuit-Available/dp/B088TVVNVM/ref=sr_1_4)
 * [Get FPV Store](https://www.getfpv.com/vifly-shortsaver-2-smart-smoke-stopper-xt60-xt30.html)
 * [Pyrodrone Store](https://pyrodrone.com/products/vifly-short-saver-2)
 * [Race Day Quads Store](https://www.racedayquads.com/products/vifly-short-saver-2-smoke-stopper-xt30-xt60)

This product is superior to all of its competitors for some very critical reasons. It is the only one that's actually an active electrical current sensing device, it is actually not a traditional fuse. All of the other similar products are simple self-resetting fuses.

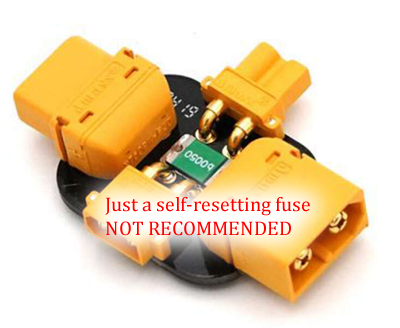
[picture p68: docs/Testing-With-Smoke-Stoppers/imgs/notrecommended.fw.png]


The problem with fuses:

First, fuses use temperature to "trip", meaning they respond slower. Instead of using a fuse, the ViFly brand uses an actual current sensor, which responds much faster, in fact, you can even configure how fast it responds.

Second, fuses that self-reset have a leakage current, meaning they don't fully protect your circuit even after they trip. These self-resetting fuses are a type of temperature dependant resistor, they increase in resistance when they get hot, which is how they stop current from flowing when they get hot. After the fuse trips, it will then cool down, and the resistance will go a bit lower, letting more current through. This could start to cause damage to your circuit. Nobody seems to make a smoke stopper with a traditional fast-blow fuse, which would require a replacement every time it blows.

The ViFly brand is not a fuse, it's more like a switch that's controlled intelligently by a current sensor, so it doesn't have this problem, once it "blows", it won't leak. To reset it, you simply press a button twice.

For $12, I hope you listen to my advice here. I know it's weird for me to praise one particular product, but it is my opinion that these advantages are actually important for true effectiveness.

There are many power supplies with current limiting that are very useful for testing robots too, but you still need to be careful, as a "current limiting" feature that delivers a constant current has the same problem as a fuse that leaks current. You want your power supply to go off and stay off until the problem is resolved.

# How to Use a Smoke Stopper

Connecting a smoke stopper is easy, it comes with a battery input connector and another output connector, usually XT30 or XT60 or both. You plug in a battery to the input, and the output connects to where your battery was supposed to go on your robot. The ViFly smoke stopper also has an ON button you need to press.

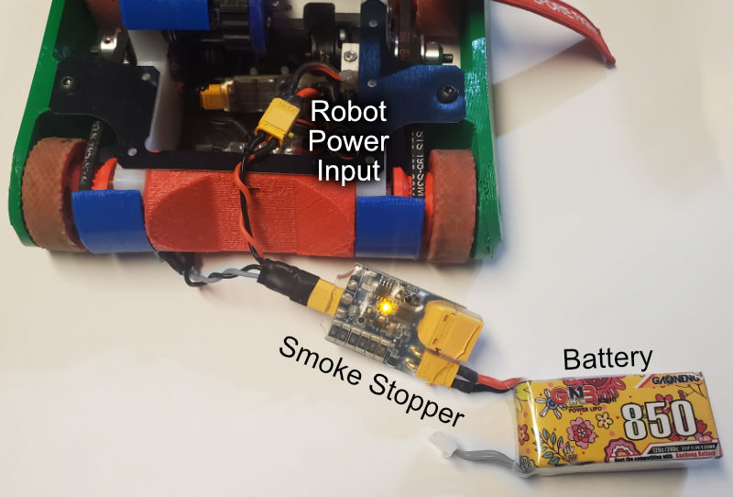
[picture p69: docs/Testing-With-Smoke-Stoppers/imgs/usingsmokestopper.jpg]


It is important to know that all of these smoke stoppers are rated or configured for only 1A of current, I think the ViFly one can be configured for 1A or 2A. This means it is not supposed to let you run motors. So basically, you are just checking things like:

 * battery did not explode
 * receiver connects to transmitter
 * lights on the ESC(s) turn on and blink

I know this won't test the motors, but your next test will be testing the motors without a smoke stopper. Using the smoke stopper was to make sure that it is safe to proceed to the next test.

# Adding USB-C to a Smoke Stopper

If you don't want to use a battery during this test, I will teach you how to power your smoke stopper with a USB-C cable instead. This is convenient because USB-C powered soldering irons and USB-C powered battery chargers are extremely popular already with the robot combat community.

You need to buy something called a "USB-C voltage trigger", which is something that tells (triggers) a USB-C power adapter to supply a higher voltage. Typically they have selectable voltages but pre-configured for 12V, which is about the same voltage as a 3S battery pack.

 * [Amazon Link, adjustable, 12V default](https://www.amazon.com/Trigger-Charging-Adjustable-Voltage-Board/dp/B0D54584JB/ref=sr_1_15)
 * [Amazon Link, adjustable, 20V default](https://www.amazon.com/Trigger-Adjustable-Voltage-Module-Default/dp/B0B688SKNK/ref=sr_1_5)
 * [Amazon Link, 12V fixed](https://www.amazon.com/AITRIP-Voltage-Trigger-Module-Type-C/dp/B09M3SQSXL/ref=sr_1_3)
 * [Amazon Link, 12V fixed](https://www.amazon.com/Trigger-Adjustable-Voltage-Module-Default/dp/B0BRNGKRDJ/ref=sr_1_5)

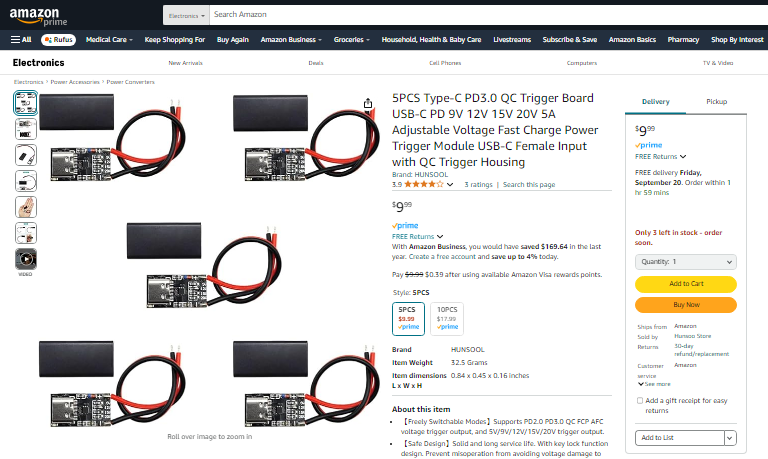
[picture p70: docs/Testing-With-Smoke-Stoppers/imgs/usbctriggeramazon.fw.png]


Get one, solder a XT30 or XT60 connector on it. Bada-bing bada-boom.

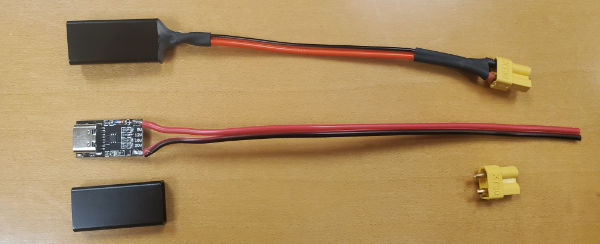
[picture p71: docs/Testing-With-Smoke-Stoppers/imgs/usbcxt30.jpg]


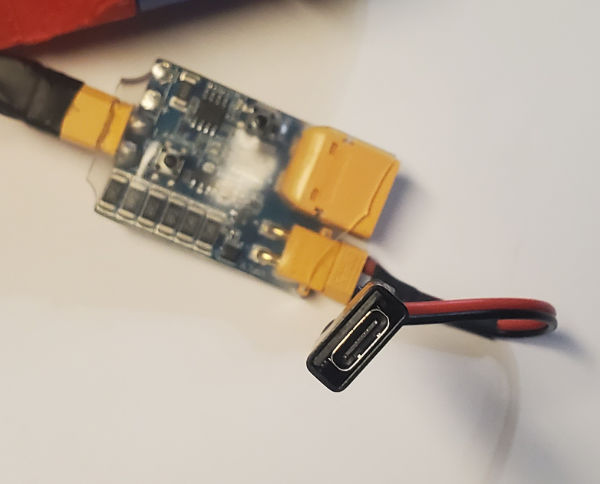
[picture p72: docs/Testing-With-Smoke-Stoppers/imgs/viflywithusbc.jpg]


Your USB-C power adapter is probably capable of outputting 2A of current at 12V, that's only about 24W. Those USB-C soldering irons use something like 65W. Remember that the smoke stopper is only 1A or 2A anyways, so it's perfectly fine to use a USB-C power adapter for these tests.

IMPORTANT: The USB-C power adapter must be capable of USB-PD and capable of 30W or more. If you can run a soldering iron with it, then it should work.

# Using a Battery Charger as a Testing Power Supply

I have a SkyRC B6neo, it's a compact battery charger powered by USB-C.

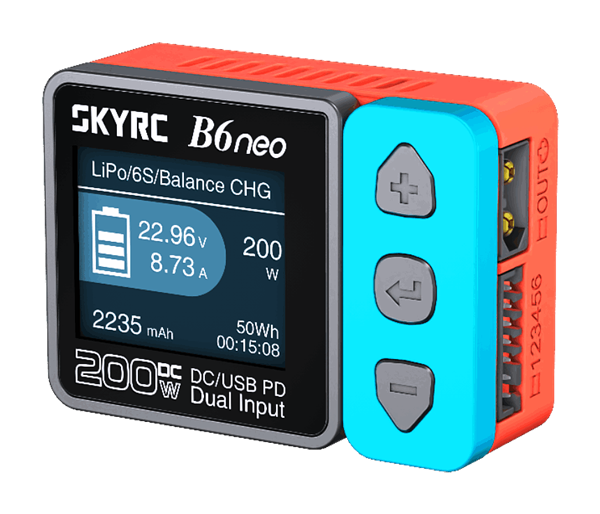
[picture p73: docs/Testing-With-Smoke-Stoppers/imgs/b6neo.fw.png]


It has an extra function, you can use it to act as a adjustable voltage power supply, with a specified current limit. Here is how to access this feature (screen shot from user manual):

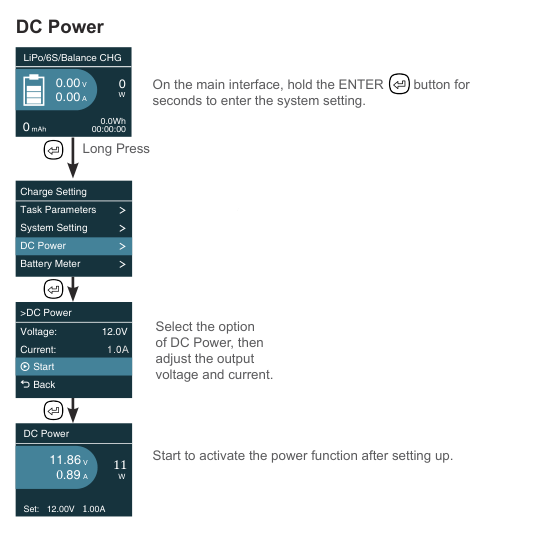
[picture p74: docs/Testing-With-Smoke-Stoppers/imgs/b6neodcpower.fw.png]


If you are unsure about the settings, I suggest you use 12V and 1.0A as the setting, which approximates a 3S battery. The current should not be too high, so 1.0A is a nice setting.

You will need to make adapter cables to use the charger this way. The end that goes into the charger must be a XT-60 female, and the other end should be the same as the connector that's already on your battery.

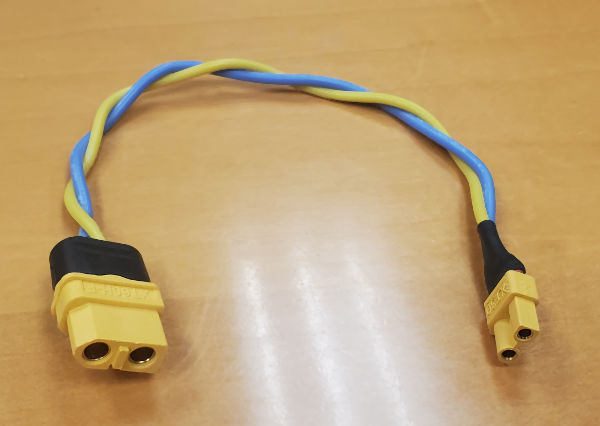
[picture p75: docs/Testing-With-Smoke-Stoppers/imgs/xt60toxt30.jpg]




If your circuit malfunctions and draws an unexpectedly large electrical current, the B6neo will show an error message and shutdown



but it might also simply shutdown without showing an error message at all. It depends on how bad the failure really was. A full short circuit will cause a shutdown without an error message, probably because the power supply upstream from the B6neo has shutdown.

**IMPORTANT: I tried both the HOTA brand and the ToolKitRC brand chargers, they should not be used as a smoke stopper**. They have constant current implementations with (what appears to be) a PID loop modulating the voltage to keep the current constantly at whatever you've set. This means it will still attempt to leak power into a circuit that is failing, it will not stop the power completely, it will not show any error messages. **Although this does actually mean they are technically better chargers than the SkyRC one. In fact, the HOTA has both constant current and constant power if you need it.**

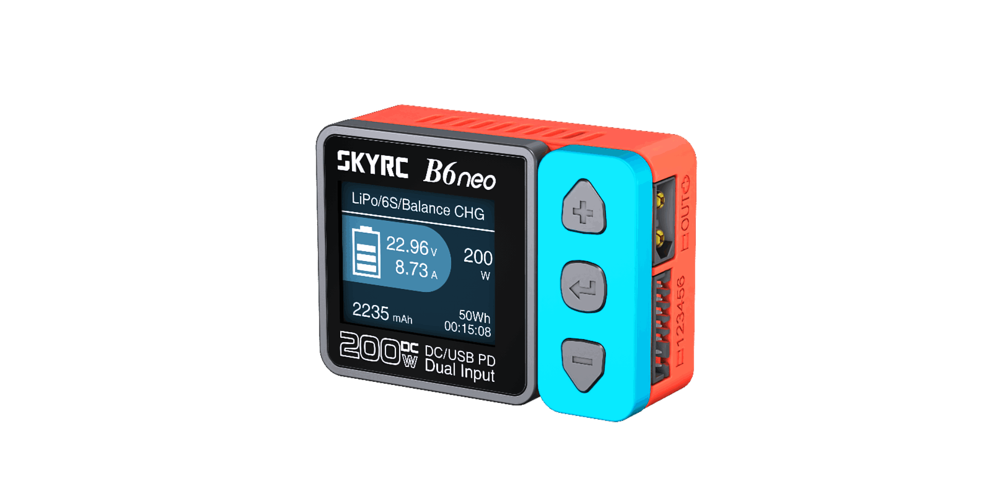
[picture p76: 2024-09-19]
docs/Testing-With-Smoke-Stoppers/imgs/top13.png

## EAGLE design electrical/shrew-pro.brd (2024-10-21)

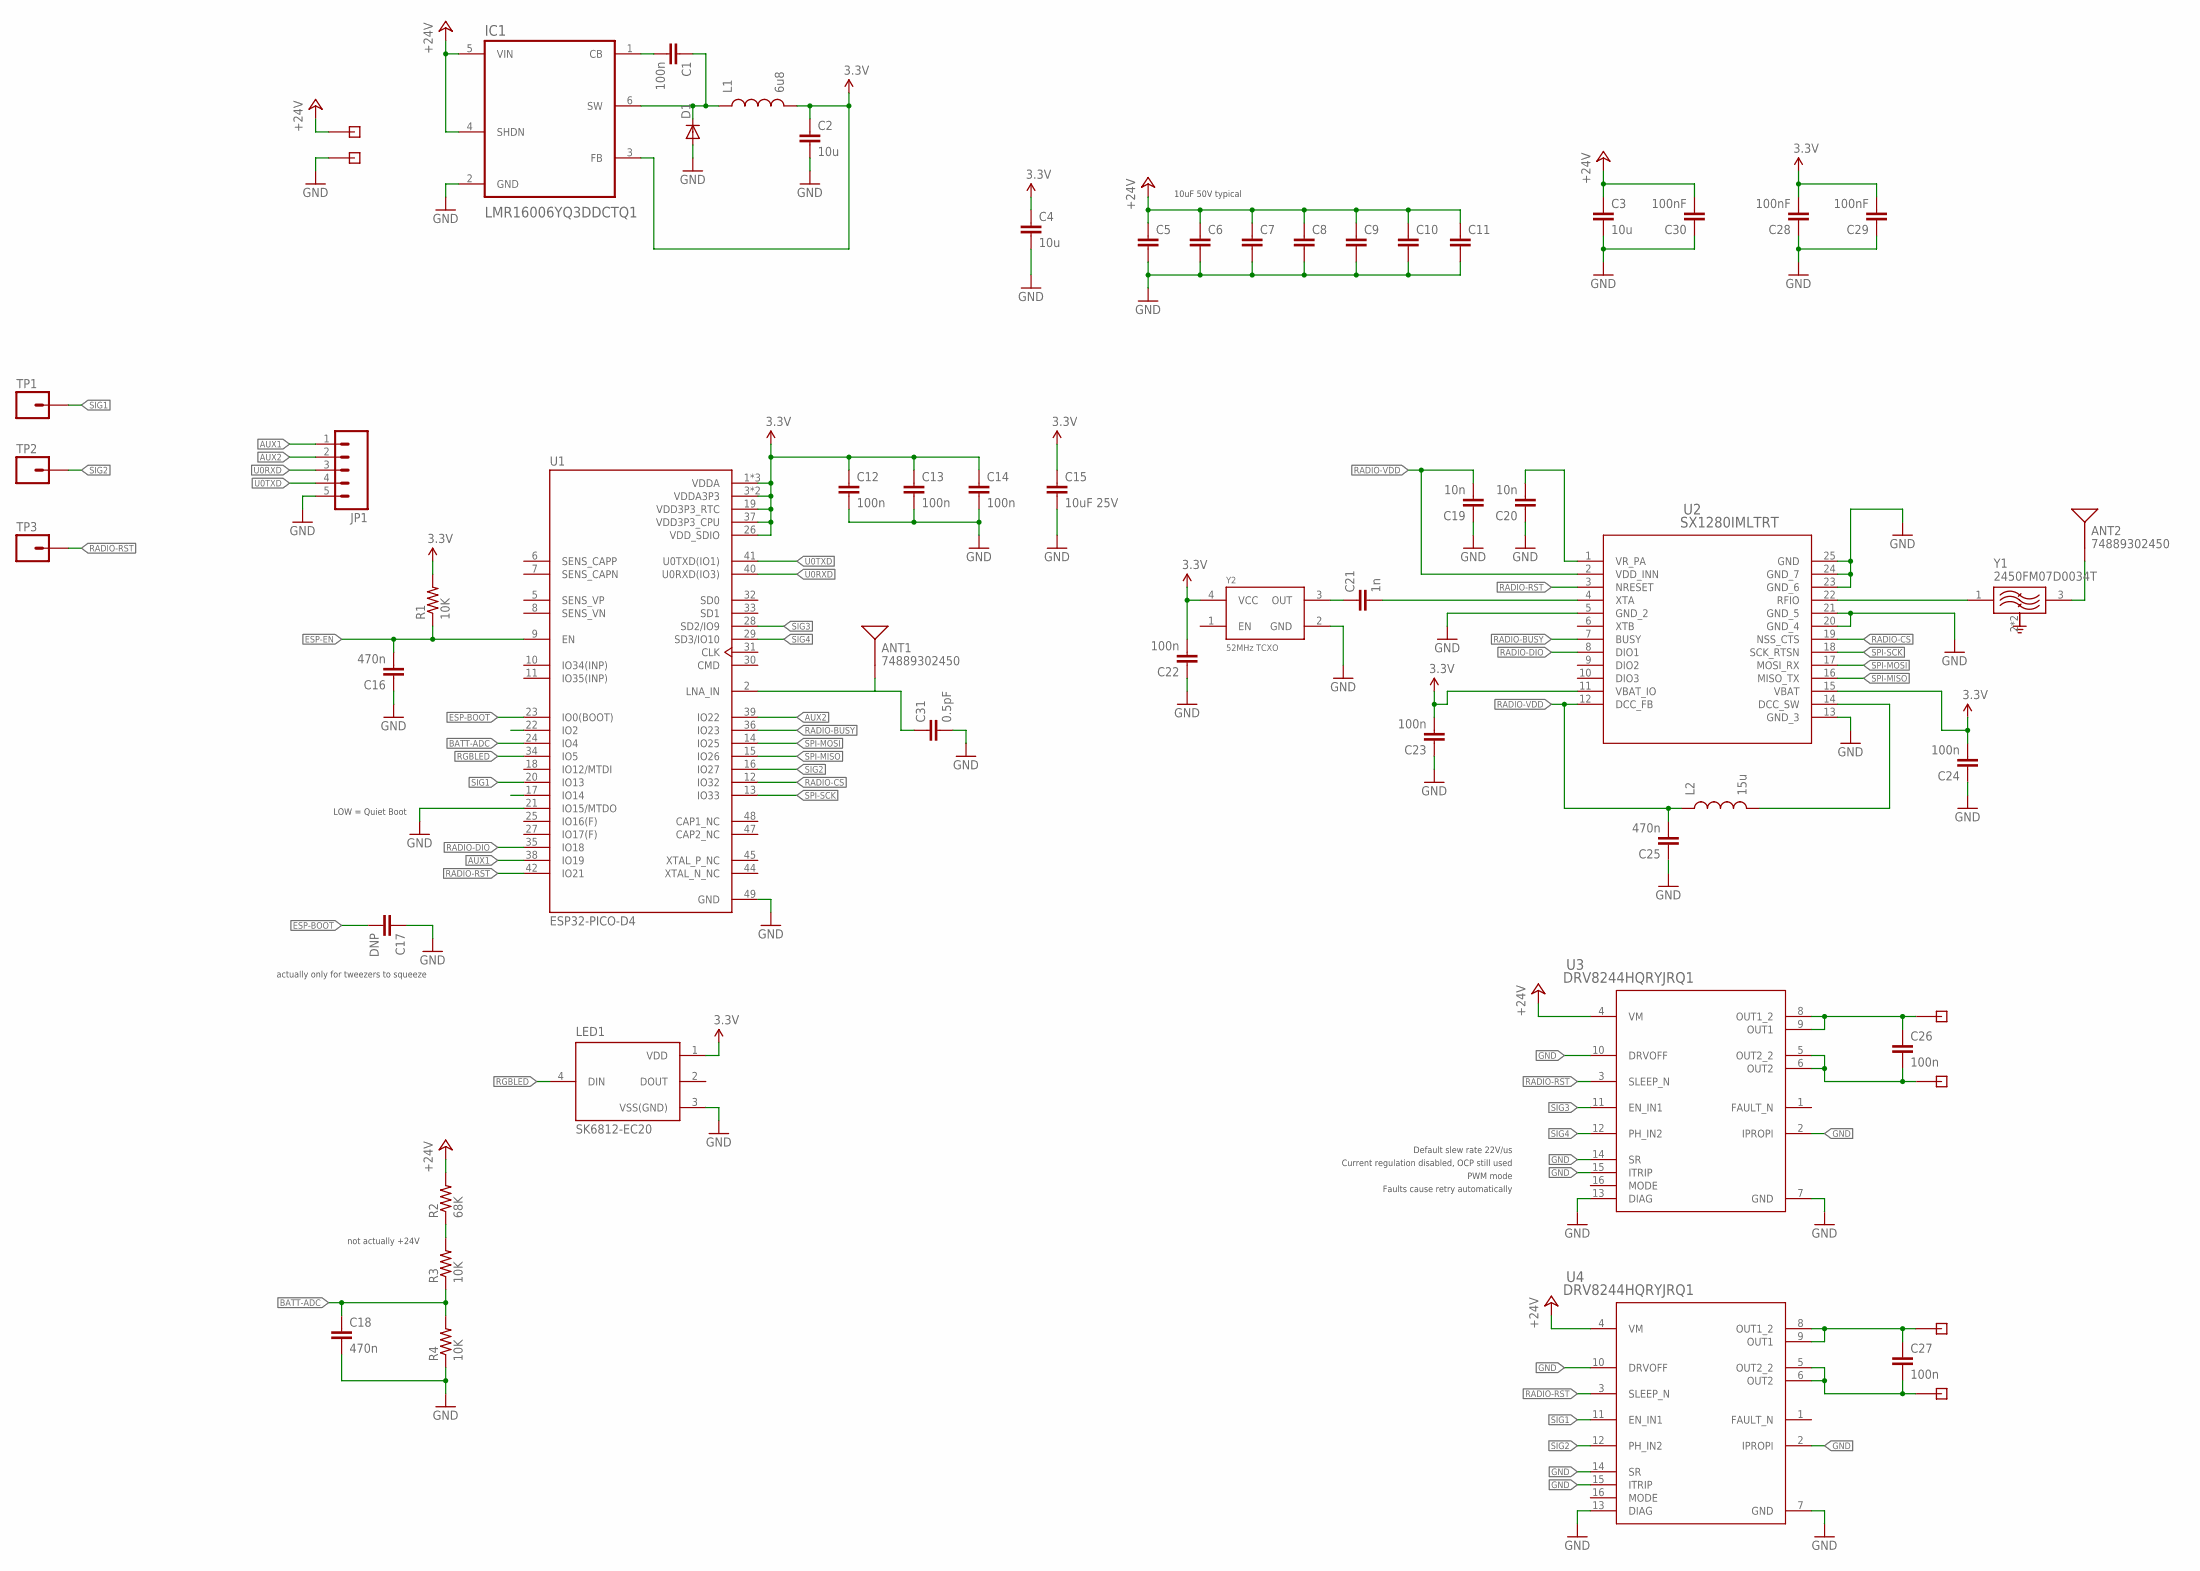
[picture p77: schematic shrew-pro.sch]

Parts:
ANT1, ANT2: 74889302450; ANTENNA-CHIP2
C1, C12, C13, C14, C22, C23, C24: 100n; 0402-REV
C2, C3, C4, C5, C6, C7, C8, C9, C10, C11: 10u; 0805
C15: 10uF 25V; 0805
C16, C18, C25: 470n; 0402-REV
C17: DNP; 0402-CAP
C19, C20: 10n; 0402-REV
C21: 1n; 0402-REV
C26, C27: 100n; 0402-CAP
C28, C29: 100nF; 0402-CAP
C30: 100nF; 0402-REV
C31: 0.5pF; 0402-CAP
D1: DIODESOD; SOD-323
IC1: LMR16006YQ3DDCTQ1; SOT95P280X110-6N
JP1: M05PTH; 1X05
L1: 6u8; 0805
L2: 15u; 0805
LED1: SK6812-EC20
R1, R3, R4: 10K; 0402-REV
R2: 68K; 0402-REV
TP1, TP2, TP3: M01-1.0MM-TP; 1X01-1.0MM-TP
U1: ESP32-PICO-D4; PQFN50P700X700X104-49N
U2: SX1280IMLTRT; QFN24_4X4_SEM
U3, U4: DRV8244HQRYJRQ1; RYJ0016A-MFG
X1, X2, X3, X4, X5, X6: PIN-1X-BIG; PAD-1X-BIG
Y1: 2450FM07D0034T; FIL_2450FM07D0034T
Y2: 52MHz TCXO; OSC_TG2016SMN_50.0000M-ECGNNMB

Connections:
3.3V: C2.1, C4.1, C12.1, C13.1, C14.1, C15.1, C22.2, C23.2, C24.2, C28.2, C29.2, IC1.3 (FB), L1.2, LED1.1 (VDD), R1.2, U1.1 (VDDA), U1.3 (VDDA3P3), U1.4 (VDDA3P3), U1.19 (VDD3P3_RTC), U1.26 (VDD_SDIO), U1.37 (VDD3P3_CPU), U1.43 (VDDA), U1.46 (VDDA), U2.11 (VBAT_IO), U2.15 (VBAT), Y2.4 (VCC)
+24V: C3.1, C5.1, C6.1, C7.1, C8.1, C9.1, C10.1, C11.1, C30.2, IC1.4 (SHDN), IC1.5 (VIN), R2.2, U3.4 (VM), U4.4 (VM), X1.1
AUX1: JP1.1, U1.38 (IO19)
AUX2: JP1.2, U1.39 (IO22)
BATT-ADC: C18.1, R3.1, R4.2, U1.24 (IO4)
ESP-BOOT: C17.2, U1.23 (IO0(BOOT))
ESP-EN: C16.2, R1.1, U1.9 (EN)
GND: C2.2, C3.2, C4.2, C5.2, C6.2, C7.2, C8.2, C9.2, C10.2, C11.2, C12.2, C13.2, C14.2, C15.2, C16.1, C17.1, C18.2, C19.1, C20.1, C22.1, C23.1, C24.1, C25.1, C28.1, C29.1, C30.1, C31.2, D1.2 (A), IC1.2 (GND), JP1.5, LED1.3 (VSS(GND)), R4.1, U1.21 (IO15/MTDO), U1.49 (GND), U2.5 (GND_2), U2.13 (GND_3), U2.20 (GND_4), U2.21 (GND_5), U2.23 (GND_6), U2.24 (GND_7), U2.25 (GND), U3.2 (IPROPI), U3.7 (GND), U3.10 (DRVOFF), U3.13 (DIAG), U3.14 (SR), U3.15 (ITRIP), U4.2 (IPROPI), U4.7 (GND), U4.10 (DRVOFF), U4.13 (DIAG), U4.14 (SR), U4.15 (ITRIP), X2.1, Y1.2 (GND), Y1.4 (GND), Y2.2 (GND)
MOTOR1: C26.1, U3.8 (OUT1_2), U3.9 (OUT1), X3.1
MOTOR2: C26.2, U3.5 (OUT2_2), U3.6 (OUT2), X4.1
MOTOR3: C27.1, U4.8 (OUT1_2), U4.9 (OUT1), X5.1
MOTOR4: C27.2, U4.5 (OUT2_2), U4.6 (OUT2), X6.1
unnamed: ANT1.FEED, C31.1, U1.2 (LNA_IN)
unnamed: C21.1, Y2.3 (OUT)
unnamed: C21.2, U2.4 (XTA)
unnamed: C1.2, IC1.1 (CB)
unnamed: U2.22 (RFIO), Y1.1 (IN)
unnamed: ANT2.FEED, Y1.3 (OUT)
unnamed: L2.2, U2.14 (DCC_SW)
unnamed: C1.1, D1.1 (C), IC1.6 (SW), L1.1
unnamed: C20.2, U2.1 (VR_PA)
RADIO-BUSY: U1.36 (IO23), U2.7 (BUSY)
RADIO-CS: U1.12 (IO32), U2.19 (NSS_CTS)
RADIO-DIO: U1.35 (IO18), U2.8 (DIO1)
RADIO-RST: TP3.1, U1.42 (IO21), U2.3 (NRESET), U3.3 (SLEEP_N), U4.3 (SLEEP_N)
RADIO-VDD: C19.2, C25.2, L2.1, U2.2 (VDD_INN), U2.12 (DCC_FB)
RGBLED: LED1.4 (DIN), U1.34 (IO5)
SIG1: TP1.1, U1.20 (IO13), U4.11 (EN_IN1)
SIG2: TP2.1, U1.16 (IO27), U4.12 (PH_IN2)
SIG3: U1.28 (SD2/IO9), U3.11 (EN_IN1)
SIG4: U1.29 (SD3/IO10), U3.12 (PH_IN2)
SPI-MISO: U1.15 (IO26), U2.16 (MISO_TX)
SPI-MOSI: U1.14 (IO25), U2.17 (MOSI_RX)
SPI-SCK: U1.13 (IO33), U2.18 (SCK_RTSN)
U0RXD: JP1.3, U1.40 (U0RXD(IO3))
U0TXD: JP1.4, U1.41 (U0TXD(IO1))
V-ADC: R2.1, R3.2

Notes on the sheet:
actually only for tweezers to squeeze
not actually +24V
LOW = Quiet Boot
10uF 50V typical
Default slew rate 22V/us
Current regulation disabled, OCP still used
PWM mode
Faults cause retry automatically

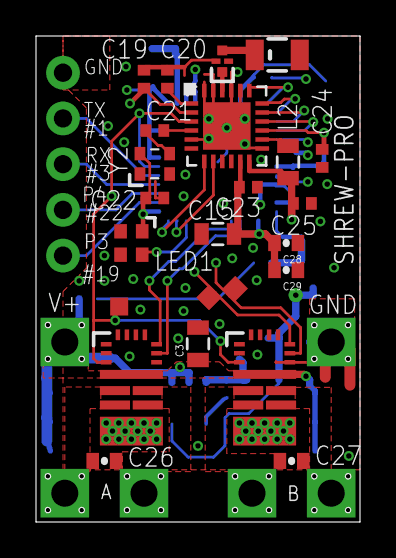
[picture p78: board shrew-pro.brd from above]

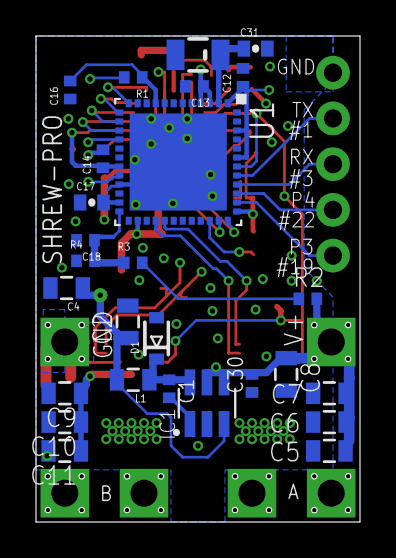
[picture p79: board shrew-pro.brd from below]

Board: 4 copper layers, 18.0 x 27.0 mm, 58 parts (27 on the bottom side), 37 nets.

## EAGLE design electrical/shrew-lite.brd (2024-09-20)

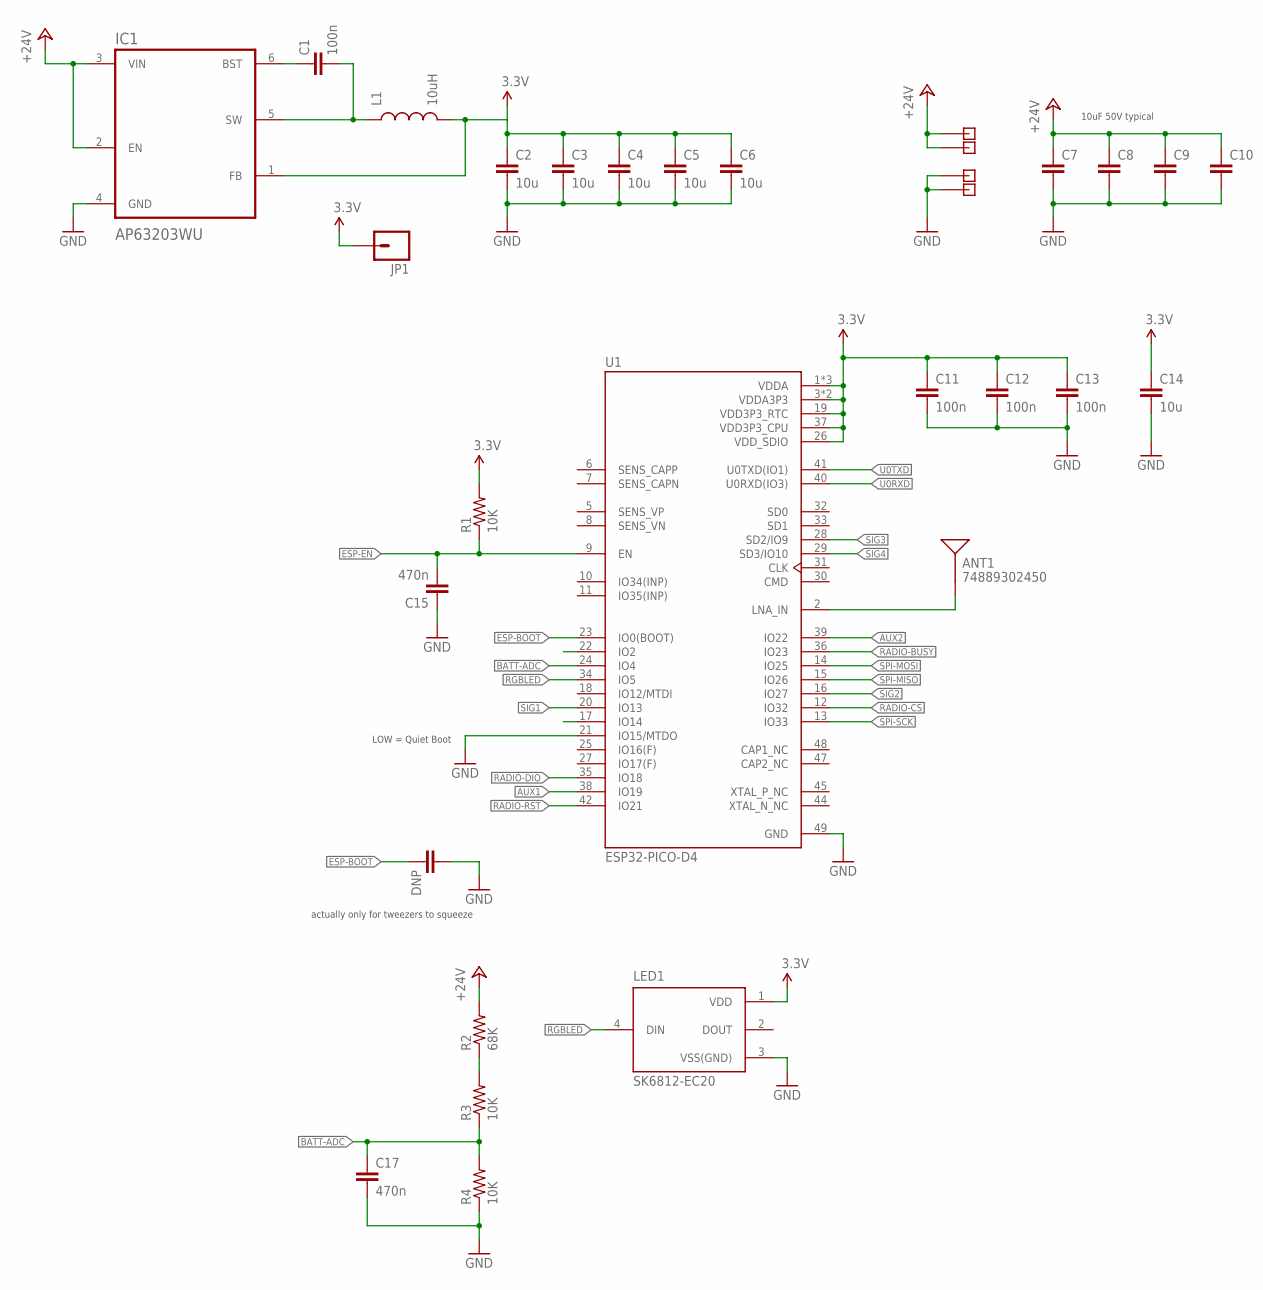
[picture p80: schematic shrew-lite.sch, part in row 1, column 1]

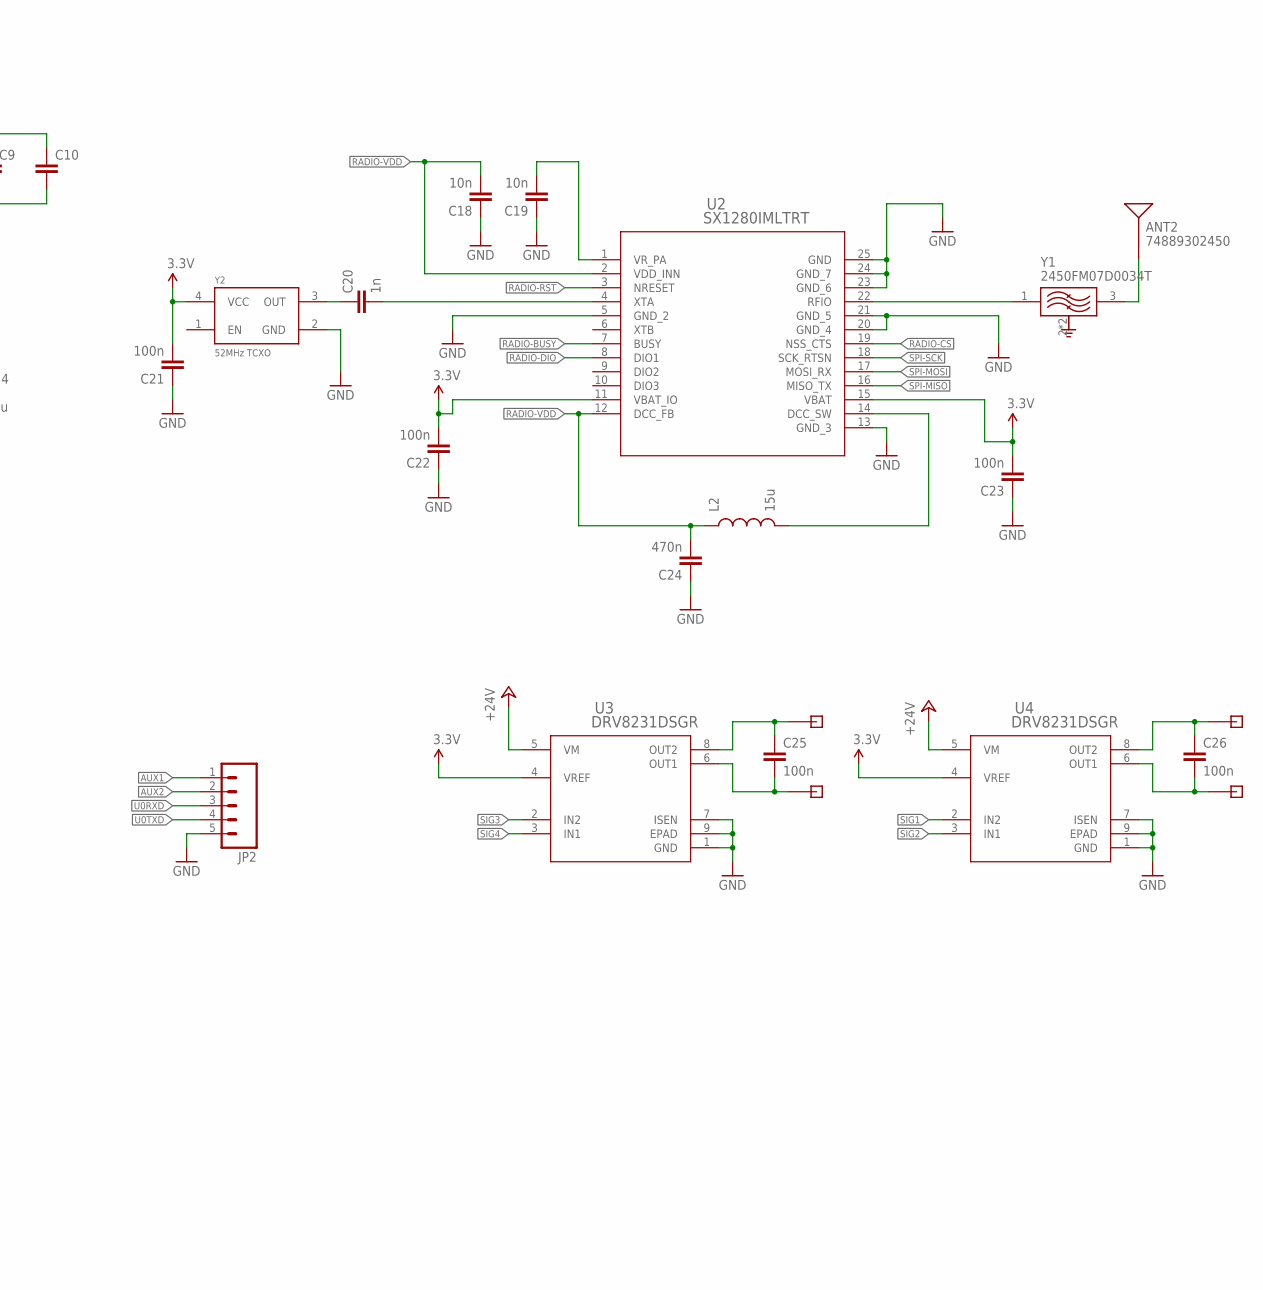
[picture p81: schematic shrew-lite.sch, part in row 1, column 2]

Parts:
ANT1, ANT2: 74889302450; ANTENNA-CHIP2
C1, C11, C12, C13, C21, C22, C23: 100n; 0402-REV
C2, C3, C4, C5, C6, C14: 10u; 0402-REV
C7, C8, C9, C10: 10u; 0805
C15, C17, C24: 470n; 0402-REV
C16: DNP; 0402-CAP
C18, C19: 10n; 0402-REV
C20: 1n; 0402-REV
C25, C26: 100n; 0402-CAP
IC1: AP63203WU; SOT95P280X110-6N
JP1: M01-1.0MM-TP; 1X01-1.0MM-TP
JP2: M05PTH; 1X05
L1: 10uH; 0805
L2: 15u; 0805
LED1: SK6812-EC20
R1, R3, R4: 10K; 0402-REV
R2: 68K; 0402-REV
U1: ESP32-PICO-D4; PQFN50P700X700X104-49N
U2: SX1280IMLTRT; QFN24_4X4_SEM
U3, U4: DRV8231DSGR; WSON8_DRV8231_TEX
X1, X2, X3, X4: PIN-1X-MED; PAD-1X-MED
X5, X6, X7, X8: PIN-1X-BIG; PAD-1X-BIG
Y1: 2450FM07D0034T; FIL_2450FM07D0034T
Y2: 52MHz TCXO; OSC_TG2016SMN_50.0000M-ECGNNMB

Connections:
3.3V: C2.1, C3.1, C4.1, C5.1, C6.1, C11.1, C12.1, C13.1, C14.1, C21.2, C22.2, C23.2, IC1.1 (FB), JP1.1, L1.2, LED1.1 (VDD), R1.2, U1.1 (VDDA), U1.3 (VDDA3P3), U1.4 (VDDA3P3), U1.19 (VDD3P3_RTC), U1.26 (VDD_SDIO), U1.37 (VDD3P3_CPU), U1.43 (VDDA), U1.46 (VDDA), U2.11 (VBAT_IO), U2.15 (VBAT), U3.4 (VREF), U4.4 (VREF), Y2.4 (VCC)
+24V: C7.1, C8.1, C9.1, C10.1, IC1.2 (EN), IC1.3 (VIN), R2.2, U3.5 (VM), U4.5 (VM), X1.1, X2.1
AUX1: JP2.1, U1.38 (IO19)
AUX2: JP2.2, U1.39 (IO22)
BATT-ADC: C17.1, R3.1, R4.2, U1.24 (IO4)
ESP-BOOT: C16.2, U1.23 (IO0(BOOT))
ESP-EN: C15.2, R1.1, U1.9 (EN)
GND: C2.2, C3.2, C4.2, C5.2, C6.2, C7.2, C8.2, C9.2, C10.2, C11.2, C12.2, C13.2, C14.2, C15.1, C16.1, C17.2, C18.1, C19.1, C21.1, C22.1, C23.1, C24.1, IC1.4 (GND), JP2.5, LED1.3 (VSS(GND)), R4.1, U1.21 (IO15/MTDO), U1.49 (GND), U2.5 (GND_2), U2.13 (GND_3), U2.20 (GND_4), U2.21 (GND_5), U2.23 (GND_6), U2.24 (GND_7), U2.25 (GND), U3.1 (GND), U3.7 (ISEN), U3.9 (EPAD), U4.1 (GND), U4.7 (ISEN), U4.9 (EPAD), X3.1, X4.1, Y1.2 (GND), Y1.4 (GND), Y2.2 (GND)
MOTOR1: C26.2, U4.6 (OUT1), X8.1
MOTOR2: C26.1, U4.8 (OUT2), X6.1
MOTOR3: C25.2, U3.6 (OUT1), X7.1
MOTOR4: C25.1, U3.8 (OUT2), X5.1
unnamed: ANT1.FEED, U1.2 (LNA_IN)
unnamed: C20.1, Y2.3 (OUT)
unnamed: C20.2, U2.4 (XTA)
unnamed: R2.1, R3.2
unnamed: U2.22 (RFIO), Y1.1 (IN)
unnamed: ANT2.FEED, Y1.3 (OUT)
unnamed: L2.2, U2.14 (DCC_SW)
unnamed: C1.2, IC1.5 (SW), L1.1
unnamed: C19.2, U2.1 (VR_PA)
unnamed: C1.1, IC1.6 (BST)
RADIO-BUSY: U1.36 (IO23), U2.7 (BUSY)
RADIO-CS: U1.12 (IO32), U2.19 (NSS_CTS)
RADIO-DIO: U1.35 (IO18), U2.8 (DIO1)
RADIO-RST: U1.42 (IO21), U2.3 (NRESET)
RADIO-VDD: C18.2, C24.2, L2.1, U2.2 (VDD_INN), U2.12 (DCC_FB)
RGBLED: LED1.4 (DIN), U1.34 (IO5)
SIG1: U1.20 (IO13), U4.2 (IN2)
SIG2: U1.16 (IO27), U4.3 (IN1)
SIG3: U1.28 (SD2/IO9), U3.2 (IN2)
SIG4: U1.29 (SD3/IO10), U3.3 (IN1)
SPI-MISO: U1.15 (IO26), U2.16 (MISO_TX)
SPI-MOSI: U1.14 (IO25), U2.17 (MOSI_RX)
SPI-SCK: U1.13 (IO33), U2.18 (SCK_RTSN)
U0RXD: JP2.3, U1.40 (U0RXD(IO3))
U0TXD: JP2.4, U1.41 (U0TXD(IO1))

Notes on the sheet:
actually only for tweezers to squeeze
LOW = Quiet Boot
10uF 50V typical

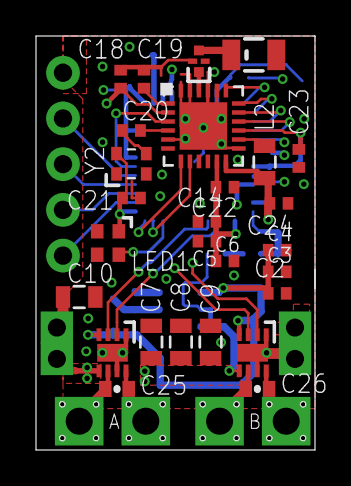
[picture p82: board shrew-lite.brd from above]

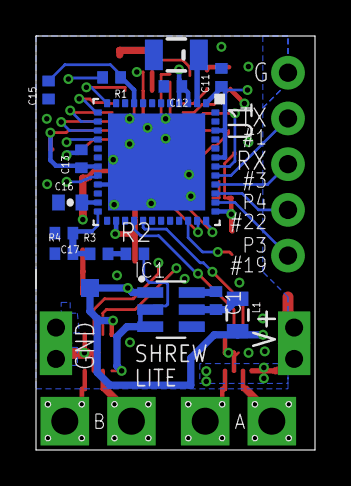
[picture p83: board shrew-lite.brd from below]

Board: 4 copper layers, 15.5 x 23.0 mm, 52 parts (16 on the bottom side), 37 nets.

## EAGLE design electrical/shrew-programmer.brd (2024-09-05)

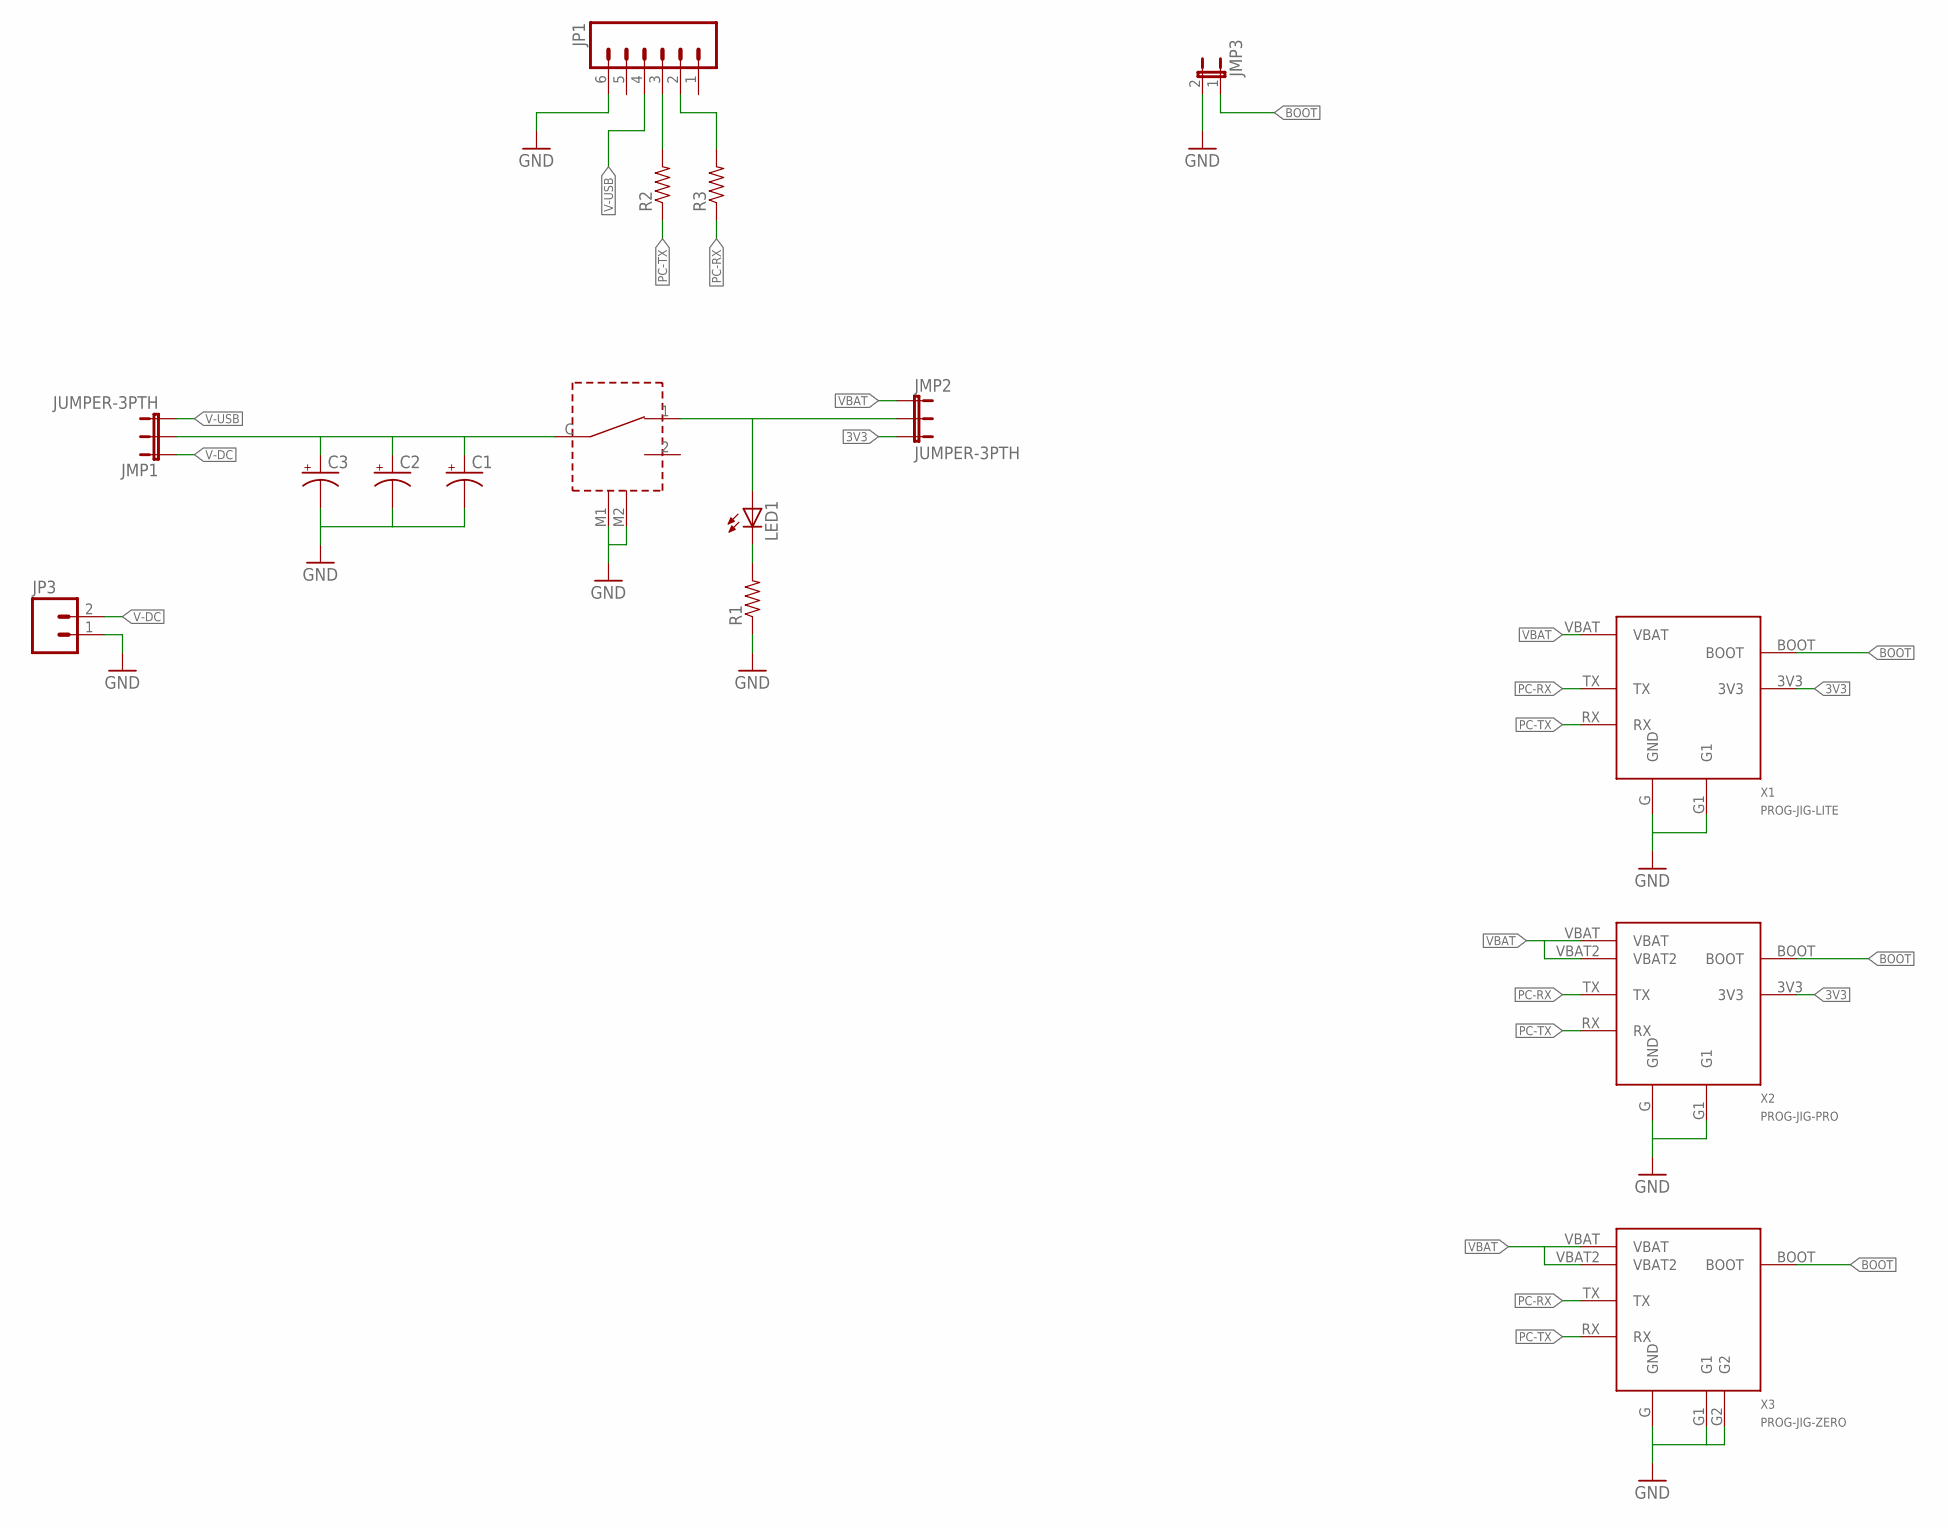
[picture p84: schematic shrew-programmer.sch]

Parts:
C1, C2, C3: CAP_POLPTH1; CPOL-RADIAL-100UF-25V
JMP1, JMP2: JUMPER-3PTH; 1X03
JMP3: JUMPER-2PTH; 1X02
JP1: M06LONGPADS; 1X06_LONGPADS
JP3: M023.5MM; SCREWTERMINAL-3.5MM-2
LED1: LED1206; LED-1206
R1, R2, R3: RESISTOR0603-RES; 0603-RES
SW1: SWITCH-ROCKER-3PIN-2MNT
X1: PROG-JIG-LITE
X2: PROG-JIG-PRO
X3: PROG-JIG-ZERO

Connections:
3V3: JMP2.3, X1.3V3, X2.3V3
BOOT: JMP3.1, X1.BOOT, X2.BOOT, X3.BOOT
GND: C1.2 (-), C2.2 (-), C3.2 (-), JMP3.2, JP1.6, JP3.1, R1.1, SW1.M1, SW1.M2, X1.G (GND), X1.G1, X2.G (GND), X2.G1, X3.G (GND), X3.G1, X3.G2
unnamed: JP1.3, R2.2
unnamed: JP1.2, R3.2
unnamed: C1.1 (+), C2.1 (+), C3.1 (+), JMP1.2, SW1.C
unnamed: LED1.C, R1.2
unnamed: JMP2.2, LED1.A, SW1.1
PC-RX: R3.1, X1.TX, X2.TX, X3.TX
PC-TX: R2.1, X1.RX, X2.RX, X3.RX
V-DC: JMP1.1, JP3.2
V-USB: JMP1.3, JP1.4
VBAT: JMP2.1, X1.VBAT, X2.VBAT, X2.VBAT2, X3.VBAT, X3.VBAT2

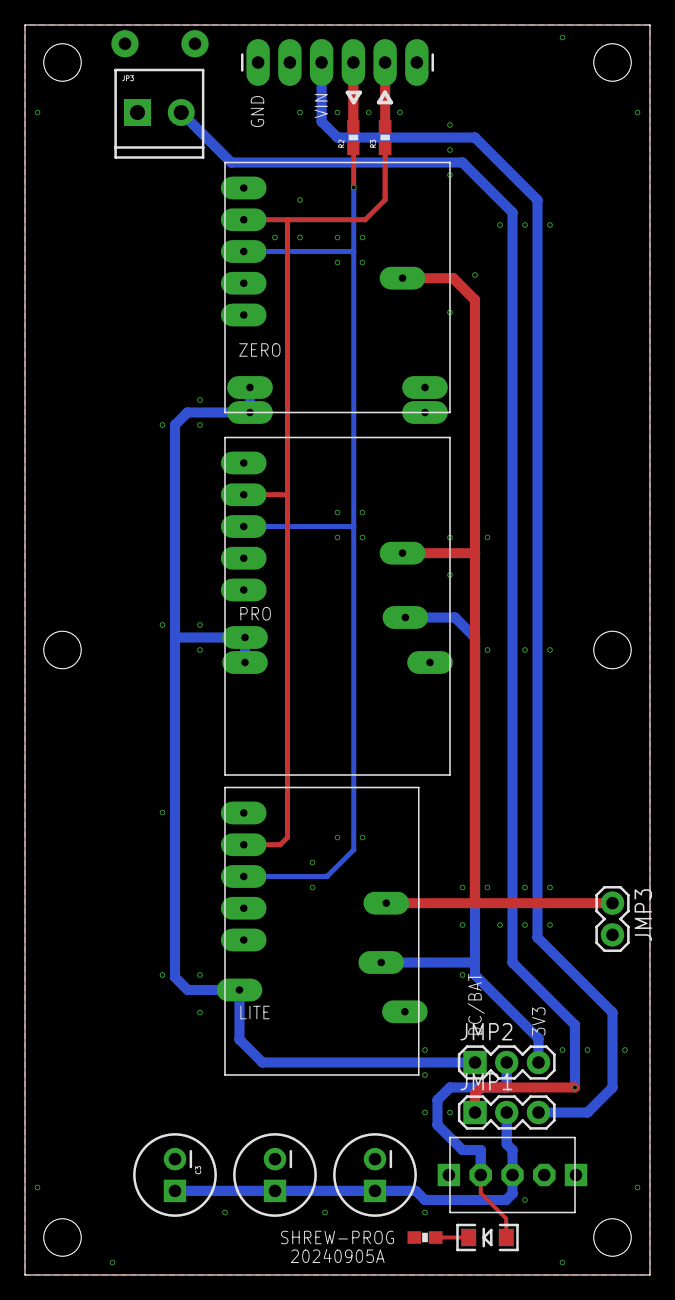
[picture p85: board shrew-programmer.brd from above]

Board: 2 copper layers, 50.0 x 100.0 mm, 16 parts (0 on the bottom side), 13 nets.

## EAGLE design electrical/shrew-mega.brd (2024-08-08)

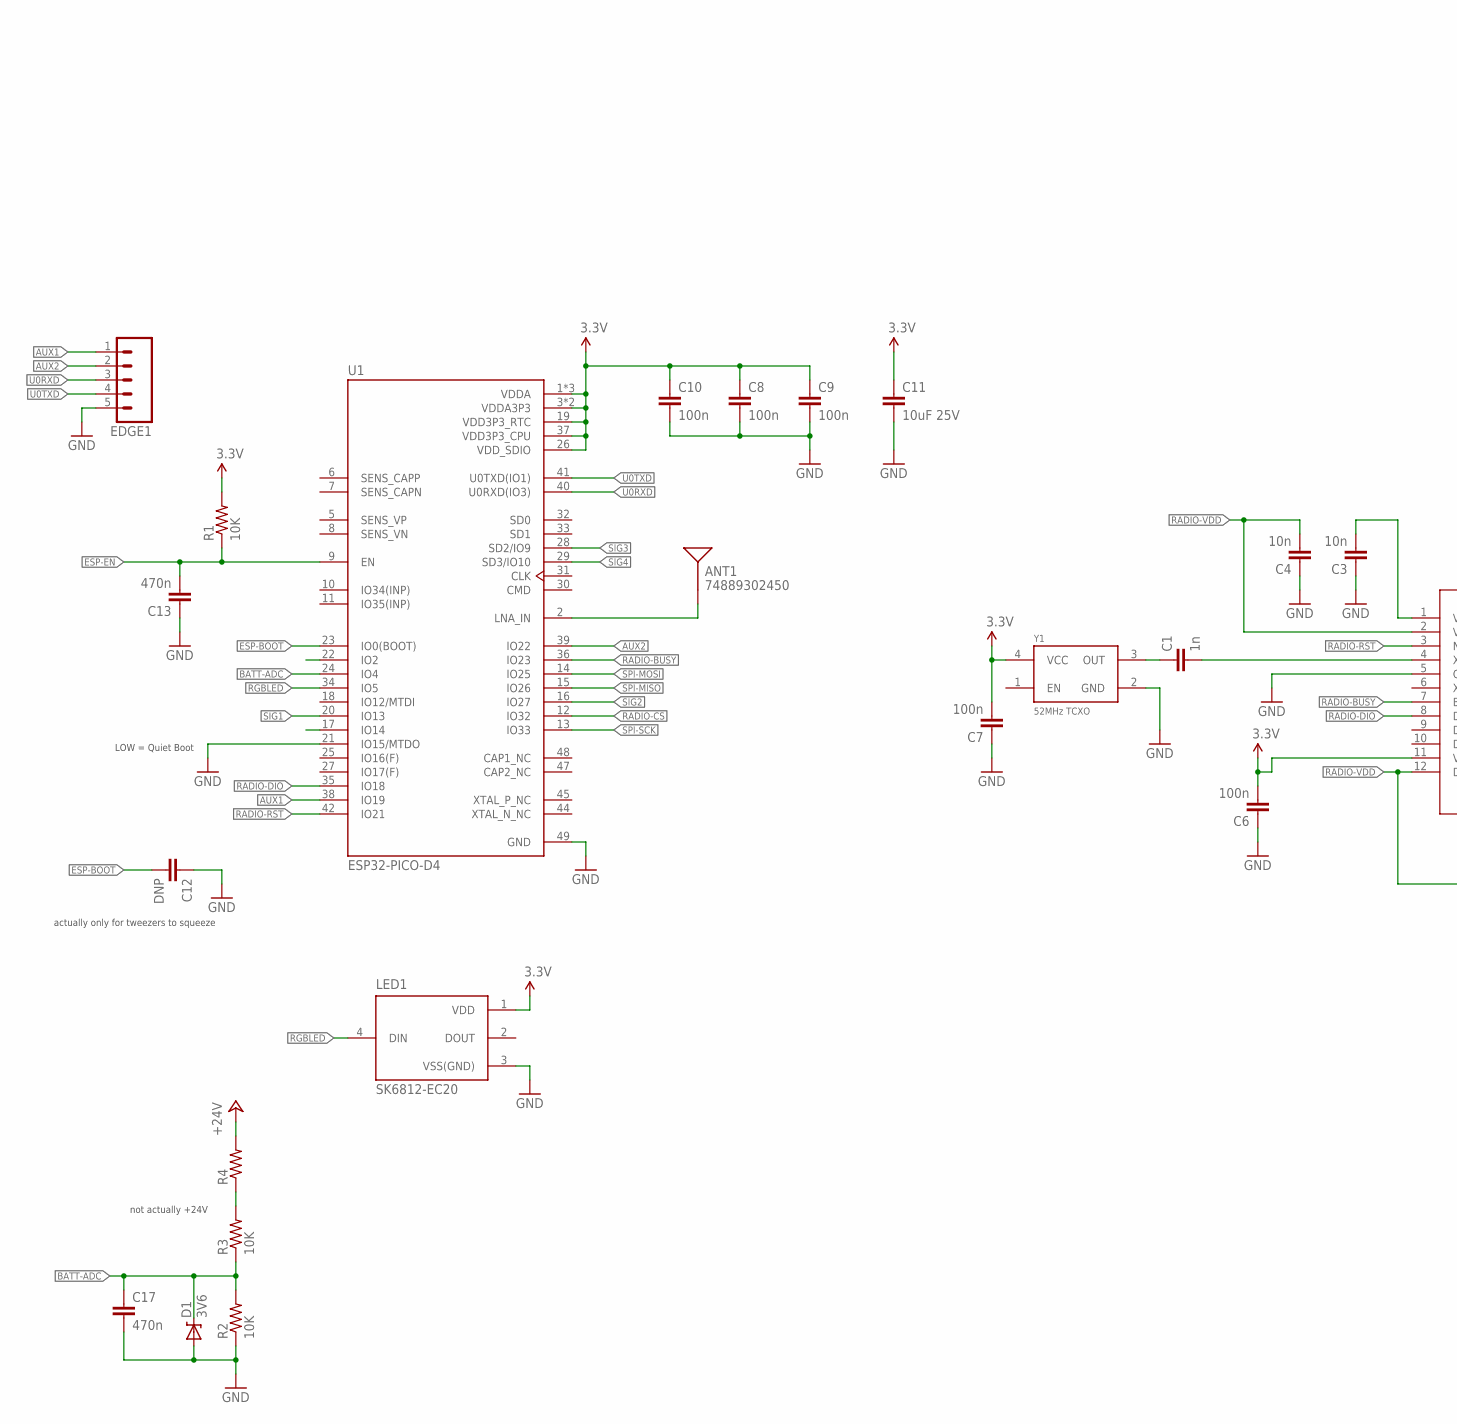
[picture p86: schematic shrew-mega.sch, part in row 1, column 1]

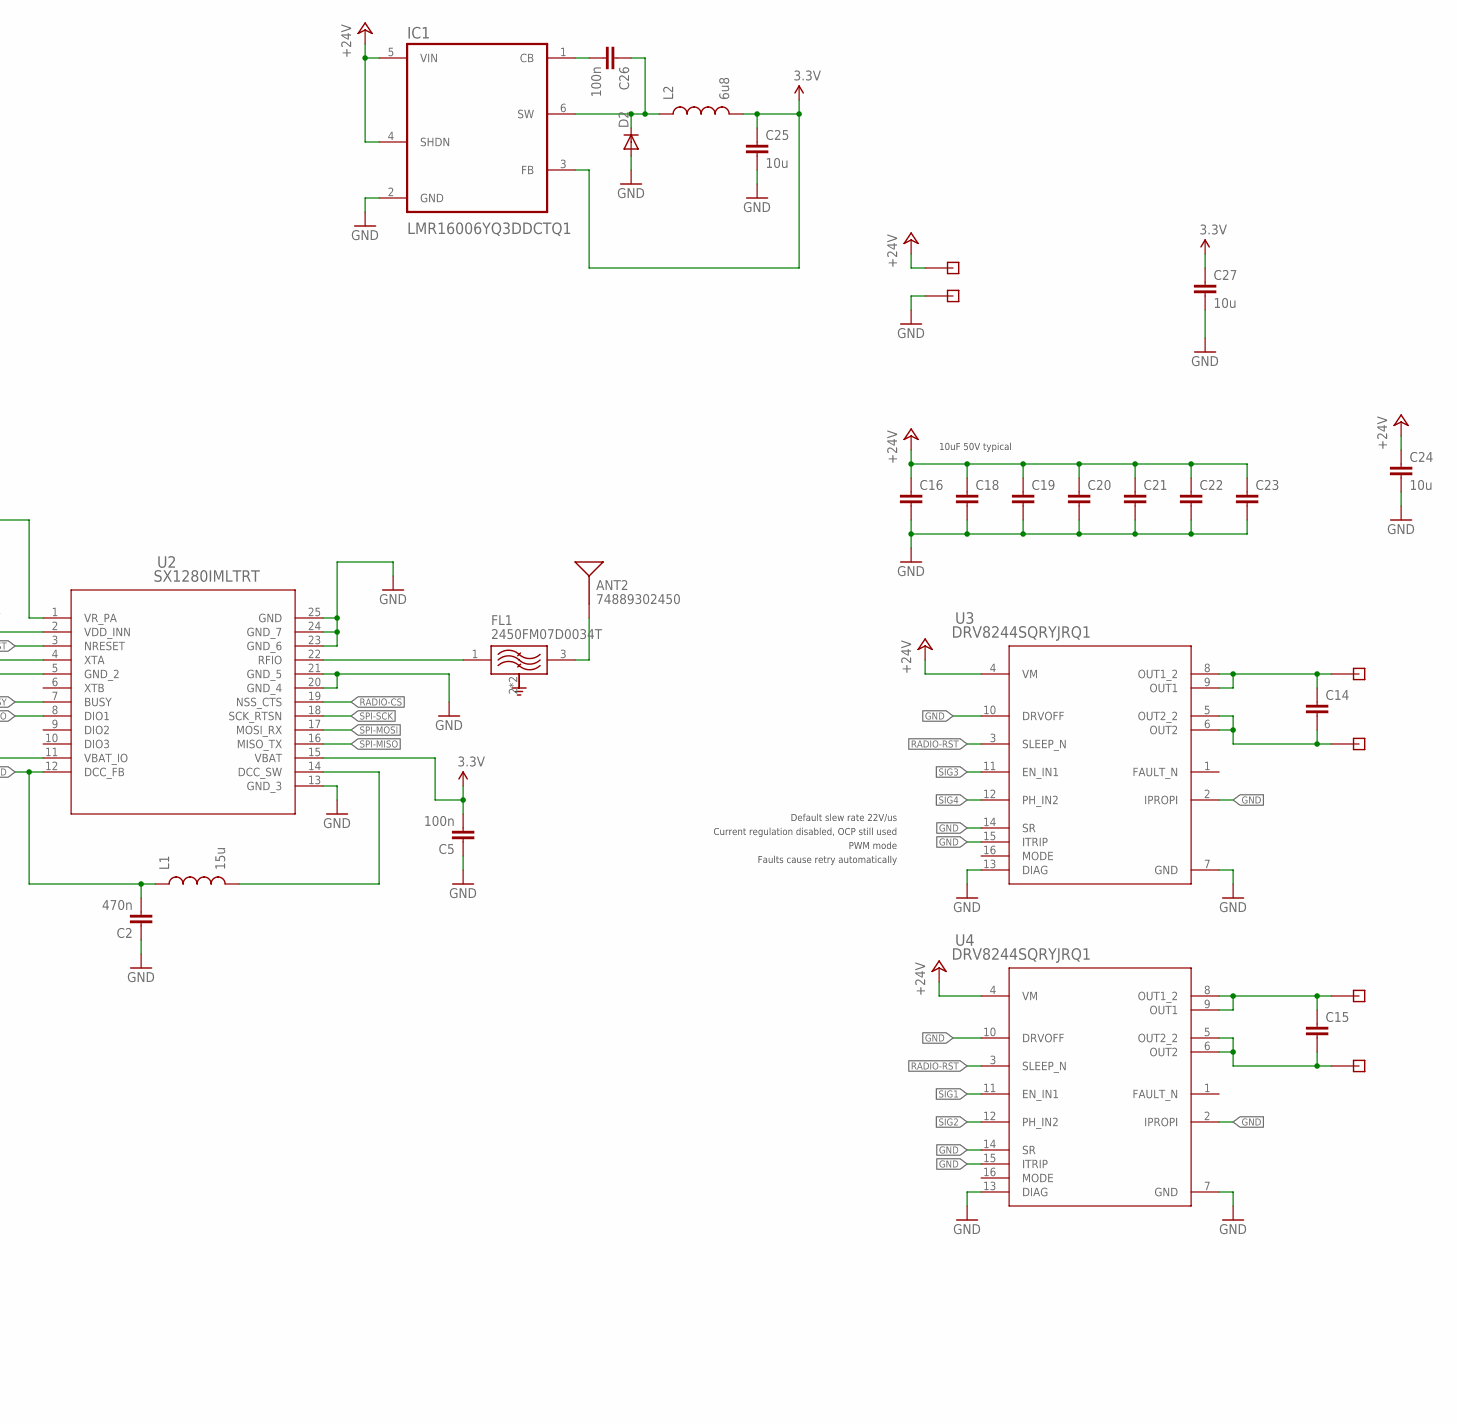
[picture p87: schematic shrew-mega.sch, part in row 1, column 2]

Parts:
ANT1, ANT2: 74889302450; ANTENNA-CHIP2
C1: 1n; 0402-REV
C2, C13, C17: 470n; 0402-REV
C3, C4: 10n; 0402-REV
C5, C6, C7, C8, C9, C10, C26: 100n; 0402-REV
C11: 10uF 25V; 0805
C12: DNP; 0402-CAP
C14, C15: CAP0402-CAP; 0402-CAP
C16, C18, C19, C20, C21, C22, C23: CAP0805; 0805
C24, C25, C27: 10u; 0805
D1: 3V6; SOD-323
D2: DIODESOD; SOD-323
EDGE1: M05PTH; 1X05
FL1: 2450FM07D0034T; FIL_2450FM07D0034T
IC1: LMR16006YQ3DDCTQ1; SOT95P280X110-6N
L1: 15u; 0805
L2: 6u8; 0805
LED1: SK6812-EC20
R1, R2, R3: 10K; 0402-REV
R4: RESISTOR0402-REV; 0402-REV
U1: ESP32-PICO-D4; PQFN50P700X700X104-49N
U2: SX1280IMLTRT; QFN24_4X4_SEM
U3, U4: DRV8244SQRYJRQ1; RYJ0016A-MFG
X1, X2, X3, X4, X5, X6: PIN-1X-BIG; PAD-1X-BIG
Y1: 52MHz TCXO; OSC_TG2016SMN_50.0000M-ECGNNMB

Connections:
3.3V: C5.2, C6.2, C7.2, C8.1, C9.1, C10.1, C11.1, C25.1, C27.1, IC1.3 (FB), L2.2, LED1.1 (VDD), R1.2, U1.1 (VDDA), U1.3 (VDDA3P3), U1.4 (VDDA3P3), U1.19 (VDD3P3_RTC), U1.26 (VDD_SDIO), U1.37 (VDD3P3_CPU), U1.43 (VDDA), U1.46 (VDDA), U2.11 (VBAT_IO), U2.15 (VBAT), Y1.4 (VCC)
+24V: C16.1, C18.1, C19.1, C20.1, C21.1, C22.1, C23.1, C24.1, IC1.4 (SHDN), IC1.5 (VIN), R4.2, U3.4 (VM), U4.4 (VM), X5.1
AUX1: EDGE1.1, U1.38 (IO19)
AUX2: EDGE1.2, U1.39 (IO22)
BATT-ADC: C17.1, D1.1 (C), R2.2, R3.1, U1.24 (IO4)
ESP-BOOT: C12.2, U1.23 (IO0(BOOT))
ESP-EN: C13.2, R1.1, U1.9 (EN)
GND: C2.1, C3.1, C4.1, C5.1, C6.1, C7.1, C8.2, C9.2, C10.2, C11.2, C12.1, C13.1, C16.2, C17.2, C18.2, C19.2, C20.2, C21.2, C22.2, C23.2, C24.2, C25.2, C27.2, D1.2 (A), D2.2 (A), EDGE1.5, FL1.2 (GND), FL1.4 (GND), IC1.2 (GND), LED1.3 (VSS(GND)), R2.1, U1.21 (IO15/MTDO), U1.49 (GND), U2.5 (GND_2), U2.13 (GND_3), U2.20 (GND_4), U2.21 (GND_5), U2.23 (GND_6), U2.24 (GND_7), U2.25 (GND), U3.2 (IPROPI), U3.7 (GND), U3.10 (DRVOFF), U3.13 (DIAG), U3.14 (SR), U3.15 (ITRIP), U4.2 (IPROPI), U4.7 (GND), U4.10 (DRVOFF), U4.13 (DIAG), U4.14 (SR), U4.15 (ITRIP), X6.1, Y1.2 (GND)
MOTOR1: C14.1, U3.8 (OUT1_2), U3.9 (OUT1), X2.1
MOTOR2: C14.2, U3.5 (OUT2_2), U3.6 (OUT2), X1.1
MOTOR3: C15.1, U4.8 (OUT1_2), U4.9 (OUT1), X4.1
MOTOR4: C15.2, U4.5 (OUT2_2), U4.6 (OUT2), X3.1
unnamed: ANT1.FEED, U1.2 (LNA_IN)
unnamed: C1.1, Y1.3 (OUT)
unnamed: C1.2, U2.4 (XTA)
unnamed: C26.2, IC1.1 (CB)
unnamed: FL1.1 (IN), U2.22 (RFIO)
unnamed: ANT2.FEED, FL1.3 (OUT)
unnamed: L1.2, U2.14 (DCC_SW)
unnamed: C26.1, D2.1 (C), IC1.6 (SW), L2.1
unnamed: C3.2, U2.1 (VR_PA)
RADIO-BUSY: U1.36 (IO23), U2.7 (BUSY)
RADIO-CS: U1.12 (IO32), U2.19 (NSS_CTS)
RADIO-DIO: U1.35 (IO18), U2.8 (DIO1)
RADIO-RST: U1.42 (IO21), U2.3 (NRESET), U3.3 (SLEEP_N), U4.3 (SLEEP_N)
RADIO-VDD: C2.2, C4.2, L1.1, U2.2 (VDD_INN), U2.12 (DCC_FB)
RGBLED: LED1.4 (DIN), U1.34 (IO5)
SIG1: U1.20 (IO13), U4.11 (EN_IN1)
SIG2: U1.16 (IO27), U4.12 (PH_IN2)
SIG3: U1.28 (SD2/IO9), U3.11 (EN_IN1)
SIG4: U1.29 (SD3/IO10), U3.12 (PH_IN2)
SPI-MISO: U1.15 (IO26), U2.16 (MISO_TX)
SPI-MOSI: U1.14 (IO25), U2.17 (MOSI_RX)
SPI-SCK: U1.13 (IO33), U2.18 (SCK_RTSN)
U0RXD: EDGE1.3, U1.40 (U0RXD(IO3))
U0TXD: EDGE1.4, U1.41 (U0TXD(IO1))
V-ADC: R3.2, R4.1

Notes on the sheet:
actually only for tweezers to squeeze
not actually +24V
LOW = Quiet Boot
10uF 50V typical
Default slew rate 22V/us
Current regulation disabled, OCP still used
PWM mode
Faults cause retry automatically

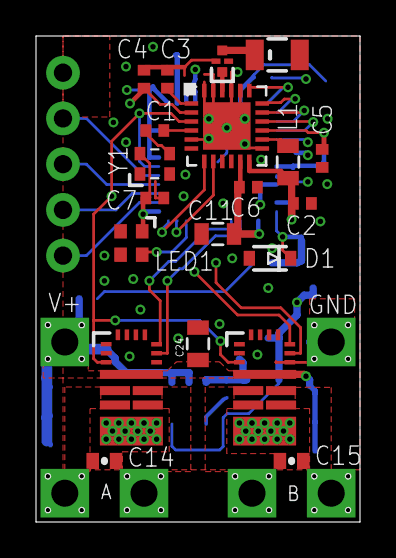
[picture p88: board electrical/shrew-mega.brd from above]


Board: 4 copper layers, 18.0 x 27.0 mm, 52 parts (25 on the bottom side), 37 nets.

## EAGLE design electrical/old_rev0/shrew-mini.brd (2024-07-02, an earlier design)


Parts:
C1, C2, C3, C4, C5: CAP0805; 0805
C6, C7: CAP0402-CAP; 0402-CAP
IC1: Vreg +3V3; SOT89
JP1: M07-2MM-TH; 1X07-2MM-TH
R1: RESISTOR0402-RES; 0402-RES
U1, U2: DRV8231DSGR; WSON8_DRV8231_TEX
X1, X2, X3, X4: PIN-1X-BIG; PAD-1X-BIG
X5: PIN-1X-1.5MMSQ; PAD-1X-1.5MMSQ
X6: PIN-1X-MED; PAD-1X-MED

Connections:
3.3V: C5.1, IC1.1 (VO), JP1.2, U1.4 (VREF), U2.4 (VREF)
+24V: C1.1, C2.1, C3.1, C4.1, IC1.3 (IN), R1.2, U1.5 (VM), U2.5 (VM), X5.P$1
GND: C1.2, C2.2, C3.2, C4.2, C5.2, IC1.2 (GND), IC1.4 (TAB), JP1.1, U1.1 (GND), U1.7 (ISEN), U1.9 (EPAD), U2.1 (GND), U2.7 (ISEN), U2.9 (EPAD), X6.P$1
MOTOR1: C7.2, U1.6 (OUT1), X3.1
MOTOR2: C7.1, U1.8 (OUT2), X4.1
MOTOR3: C6.2, U2.6 (OUT1), X1.1
MOTOR4: C6.1, U2.8 (OUT2), X2.1
SIG1: JP1.4, U1.2 (IN2)
SIG2: JP1.5, U1.3 (IN1)
SIG3: JP1.6, U2.2 (IN2)
SIG4: JP1.7, U2.3 (IN1)
V-ADC: JP1.3, R1.1

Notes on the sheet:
10uF 50V typical



Board: 2 copper layers, 14.0 x 11.0 mm, 18 parts (4 on the bottom side), 12 nets.

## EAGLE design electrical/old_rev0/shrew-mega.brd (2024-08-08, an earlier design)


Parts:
C1, C2, C3, C4, C5, C6, C7, C8, C11: CAP0805; 0805
C9, C10: CAP0402-CAP; 0402-CAP
IC1: V_REG_SOT-SOT223; SOT223
JP1: M07-2MM-TH; 1X07-2MM-TH
R1: RESISTOR0402-RES; 0402-RES
U1, U2: DRV8244SQRYJRQ1; RYJ0016A-MFG
X1, X2, X3, X4, X5, X6: PIN-1X-BIG; PAD-1X-BIG

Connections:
3.3V: C8.1, IC1.3 (VO), JP1.2
+24V: C1.1, C2.1, C3.1, C4.1, C5.1, C6.1, C7.1, C11.1, IC1.1 (IN), R1.2, U1.4 (VM), U2.4 (VM), X5.1
GND: C1.2, C2.2, C3.2, C4.2, C5.2, C6.2, C7.2, C8.2, C11.2, IC1.2 (GND), IC1.4 (TAB), JP1.1, U1.2 (IPROPI), U1.7 (GND), U1.10 (DRVOFF), U1.13 (DIAG), U1.14 (SR), U1.15 (ITRIP), U2.2 (IPROPI), U2.7 (GND), U2.10 (DRVOFF), U2.13 (DIAG), U2.14 (SR), U2.15 (ITRIP), X6.1
MOTOR1: C9.1, U1.8 (OUT1_2), U1.9 (OUT1), X2.1
MOTOR2: C9.2, U1.5 (OUT2_2), U1.6 (OUT2), X1.1
MOTOR3: C10.1, U2.8 (OUT1_2), U2.9 (OUT1), X4.1
MOTOR4: C10.2, U2.5 (OUT2_2), U2.6 (OUT2), X3.1
SIG1: JP1.4, U2.11 (EN_IN1)
SIG2: JP1.5, U2.12 (PH_IN2)
SIG3: JP1.6, U1.11 (EN_IN1)
SIG4: JP1.7, U1.12 (PH_IN2)
SLEEP: U1.3 (SLEEP_N), U2.3 (SLEEP_N)
V-ADC: JP1.3, R1.1

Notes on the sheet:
10uF 50V typical
Default slew rate 22V/us
Current regulation disabled, OCP still used
PWM mode
Faults cause retry automatically



Board: 2 copper layers, 18.0 x 15.0 mm, 22 parts (10 on the bottom side), 13 nets.

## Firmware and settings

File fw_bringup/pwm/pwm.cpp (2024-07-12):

#include <Arduino.h>

#define HBRIDGE_PIN_A1 10
#define HBRIDGE_PIN_A2 9
#define HBRIDGE_PIN_B1 19
#define HBRIDGE_PIN_B2 22
#define HBRIDGE_PWM_FREQ 24000U

void setup()
{
    pinMode(HBRIDGE_PIN_A1, OUTPUT);
    pinMode(HBRIDGE_PIN_A2, OUTPUT);
    pinMode(HBRIDGE_PIN_B1, OUTPUT);
    pinMode(HBRIDGE_PIN_B2, OUTPUT);
    analogWriteResolution(8);
    analogWriteFrequency(HBRIDGE_PWM_FREQ);
    analogWrite(HBRIDGE_PIN_A1, 0);
    analogWrite(HBRIDGE_PIN_A2, 0);
    analogWrite(HBRIDGE_PIN_B1, 0);
    analogWrite(HBRIDGE_PIN_B2, 0);
}

void loop()
{
    static uint32_t x = 0;
    uint32_t y;
    y = (x + (16 * 1)) % 256;
    analogWrite(HBRIDGE_PIN_A1, y);
    y = (x + (16 * 2)) % 256;
    analogWrite(HBRIDGE_PIN_A2, y);
    y = (x + (16 * 3)) % 256;
    analogWrite(HBRIDGE_PIN_B1, y);
    y = (x + (16 * 4)) % 256;
    analogWrite(HBRIDGE_PIN_B2, y);
    x = (x + 1) % 256;
    delay(1);
}

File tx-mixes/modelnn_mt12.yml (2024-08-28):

semver: 2.10.0
header: 
   name: "MixForMT12"
telemetryProtocol: 0
thrTrim: 0
noGlobalFunctions: 0
displayTrims: 2
ignoreSensorIds: 0
trimInc: 0
disableThrottleWarning: 1
displayChecklist: 0
extendedLimits: 0
extendedTrims: 0
throttleReversed: 0
enableCustomThrottleWarning: 0
disableTelemetryWarning: 0
showInstanceIds: 0
checklistInteractive: 0
hatsMode: TRIMS_ONLY
customThrottleWarningPosition: 0
beepANACenter: 0
mixData: 
 -
   weight: 100
   destCh: 0
   srcRaw: ch(23)
   carryTrim: 1
   mixWarn: 0
   mltpx: ADD
   offset: 0
   swtch: "NONE"
   flightModes: 000000000
   curve: 
      type: 3
      value: 28
   delayUp: 0
   delayDown: 0
   speedUp: 0
   speedDown: 0
   name: "LAdz"
 -
   weight: 100
   destCh: 1
   srcRaw: ch(24)
   carryTrim: 1
   mixWarn: 0
   mltpx: ADD
   offset: 0
   swtch: "NONE"
   flightModes: 000000000
   curve: 
      type: 3
      value: 28
   delayUp: 0
   delayDown: 0
   speedUp: 0
   speedDown: 0
   name: "RAdz"
 -
   weight: 100
   destCh: 2
   srcRaw: ch(19)
   carryTrim: 1
   mixWarn: 0
   mltpx: REPL
   offset: 0
   swtch: "NONE"
   flightModes: 000000000
   delayUp: 0
   delayDown: 0
   speedUp: 20
   speedDown: 0
   name: "WEAP"
 -
   weight: 100
   destCh: 19
   srcRaw: I2
   carryTrim: 1
   mixWarn: 0
   mltpx: REPL
   offset: 0
   swtch: "NONE"
   flightModes: 000000000
   curve: 
      type: 3
      value: 26
   delayUp: 0
   delayDown: 0
   speedUp: 0
   speedDown: 0
   name: "WEAP"
 -
   weight: 100
   destCh: 19
   srcRaw: I1
   carryTrim: 1
   mixWarn: 0
   mltpx: MUL
   offset: 0
   swtch: "L56"
   flightModes: 000000000
   curve: 
      type: 3
      value: 27
   delayUp: 0
   delayDown: 0
   speedUp: 0
   speedDown: 0
   name: "WepSlo"
 -
   weight: 0
   destCh: 19
   srcRaw: MAX
   carryTrim: 1
   mixWarn: 0
   mltpx: REPL
   offset: 0
   swtch: "L57"
   flightModes: 000000000
   delayUp: 0
   delayDown: 0
   speedUp: 0
   speedDown: 0
   name: ""
 -
   weight: 100
   destCh: 23
   srcRaw: ch(30)
   carryTrim: 1
   mixWarn: 0
   mltpx: REPL
   offset: 0
   swtch: "NONE"
   flightModes: 000000000
   delayUp: 0
   delayDown: 0
   speedUp: 0
   speedDown: 0
   name: "Drv-L"
 -
   weight: 100
   destCh: 23
   srcRaw: ch(31)
   carryTrim: 1
   mixWarn: 0
   mltpx: ADD
   offset: 0
   swtch: "NONE"
   flightModes: 000000000
   delayUp: 0
   delayDown: 0
   speedUp: 0
   speedDown: 0
   name: "Mix"
 -
   weight: 100
   destCh: 23
   srcRaw: ch(28)
   carryTrim: 1
   mixWarn: 0
   mltpx: MUL
   offset: 0
   swtch: "NONE"
   flightModes: 000000000
   delayUp: 0
   delayDown: 0
   speedUp: 0
   speedDown: 0
   name: "Bias"
 -
   weight: 100
   destCh: 23
   srcRaw: ch(26)
   carryTrim: 1
   mixWarn: 0
   mltpx: MUL
   offset: 0
   swtch: "NONE"
   flightModes: 000000000
   delayUp: 0
   delayDown: 0
   speedUp: 0
   speedDown: 0
   name: "Speed"
 -
   weight: -400
   destCh: 23
   srcRaw: ls(58)
   carryTrim: 1
   mixWarn: 0
   mltpx: MUL
   offset: 0
   swtch: "NONE"
   flightModes: 000000000
   delayUp: 0
   delayDown: 0
   speedUp: 0
   speedDown: 0
   name: "Flip"
 -
   weight: 100
   destCh: 24
   srcRaw: ch(30)
   carryTrim: 1
   mixWarn: 0
   mltpx: REPL
   offset: 0
   swtch: "NONE"
   flightModes: 000000000
   delayUp: 0
   delayDown: 0
   speedUp: 0
   speedDown: 0
   name: "Drv-R"
 -
   weight: -100
   destCh: 24
   srcRaw: ch(31)
   carryTrim: 1
   mixWarn: 0
   mltpx: ADD
   offset: 0
   swtch: "NONE"
   flightModes: 000000000
   delayUp: 0
   delayDown: 0
   speedUp: 0
   speedDown: 0
   name: "Mix"
 -
   weight: 100
   destCh: 24
   srcRaw: ch(29)
   carryTrim: 1
   mixWarn: 0
   mltpx: MUL
   offset: 0
   swtch: "NONE"
   flightModes: 000000000
   delayUp: 0
   delayDown: 0
   speedUp: 0
   speedDown: 0
   name: "Bias"
 -
   weight: 100
   destCh: 24
   srcRaw: ch(26)
   carryTrim: 1
   mixWarn: 0
   mltpx: MUL
   offset: 0
   swtch: "NONE"
   flightModes: 000000000
   delayUp: 0
   delayDown: 0
   speedUp: 0
   speedDown: 0
   name: "Speed"
 -
   weight: -400
   destCh: 24
   srcRaw: ls(58)
   carryTrim: 1
   mixWarn: 0
   mltpx: MUL
   offset: 0
   swtch: "NONE"
   flightModes: 000000000
   delayUp: 0
   delayDown: 0
   speedUp: 0
   speedDown: 0
   name: "Flip"
 -
   weight: 100
   destCh: 25
   srcRaw: TrimAil
   carryTrim: 1
   mixWarn: 0
   mltpx: REPL
   offset: 0
   swtch: "NONE"
   flightModes: 000000000
   curve: 
      type: 3
      value: 30
   delayUp: 0
   delayDown: 0
   speedUp: 0
   speedDown: 0
   name: "DrvSpd"
 -
   weight: 100
   destCh: 26
   srcRaw: TrimThr
   carryTrim: 1
   mixWarn: 0
   mltpx: ADD
   offset: 0
   swtch: "NONE"
   flightModes: 000000000
   curve: 
      type: 3
      value: 30
   delayUp: 0
   delayDown: 0
   speedUp: 0
   speedDown: 0
   name: "MotSpd"
 -
   weight: 100
   destCh: 27
   srcRaw: TrimEle
   carryTrim: 1
   mixWarn: 0
   mltpx: ADD
   offset: 0
   swtch: "NONE"
   flightModes: 000000000
   curve: 
      type: 3
      value: 30
   delayUp: 0
   delayDown: 0
   speedUp: 0
   speedDown: 0
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

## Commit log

2024-06-07 starting to gather parts for the pcb parts library
2024-06-09 wip, before splitting board into modules
    [shrew.brd, shrew.sch]
2024-06-09 wip, rx modularized
    [shrew-rx.brd, shrew-rx.sch]
2024-06-09 wip for rx
    [shrew-rx.brd, shrew-rx.sch]
2024-06-09 mini board
    [shrew-mini.brd, shrew-mini.sch, shrew.brd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]
2024-06-10 rx mfg file trial run
    [shrew-mega.brd, shrew-mega.sch, shrew-mini.brd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]
2024-06-10 more mfg files
    [shrew-mega-10-bottom_copper.GBL, shrew-mega-3-top_solderpaste.GTP, shrew-mega-4-top_soldermask.GTS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]
2024-06-12 changed v-reg on the mega variant to be more avail
    [shrew-mega.brd, shrew-mega.sch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]
2024-06-13 mfg file improvements, fixed drill file error
    [shrew-mega-bom.csv, shrew-mini-bom.csv, shrew-rx-bom.csv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]
2024-06-27 RX BOM and CPL update
    [shrew-rx-bom.csv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]
2024-06-29 schematic stitcher
    [shrew-mega.brd, shrew-mega.sch, shrew-mini.brd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]
2024-06-30 added better 0402 footprint to lib
2024-06-30 changed all 0402 footprints on rx
    [shrew-rx.brd, shrew-rx.sch]
2024-07-02 added power input silk
    [shrew-mega.brd, shrew-mini.brd, shrew-mini.sch]
2024-07-18 rev 0 doc, mega continuous current test
2024-08-08 initial work on integrated versions
    [shrew-mega-integrated.brd, shrew-mega-integrated.sch, shrew-mega.brd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]
2024-08-08 second gen gerbers
    [shrew-lite-10-bottom_copper.GBL, shrew-lite-3-top_solderpaste.GTP, shrew-lite-4-top_soldermask.GTS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]
2024-08-09 placed a PCBA order for shrew-lite
    [shrew-lite-bom.csv, shrew-lite.brd, shrew-lite.sch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]
2024-08-10 ordered programmer PCB
    [shrew-programmer-10-bottom_copper.GBL, shrew-programmer-3-top_solderpaste.GTP, shrew-programmer-4-top_soldermask.GTS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]
2024-08-11 added shrew-zero, fixed some inner planes to avoid antenna
    [shrew-lite.brd, shrew-pro.brd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]
2024-08-11 shrew-zero bom
    [shrew-zero-bom.csv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]
2024-08-12 shrew-zero major update
    [shrew-zero-10-bottom_copper.GBL, shrew-zero-3-top_solderpaste.GTP, shrew-zero-4-top_soldermask.GTS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]
2024-08-12 rotation of clock
    [shrew-pro-cpl.csv, shrew-zero-cpl.csv]
2024-08-15 sorted component ref des
    [shrew-lite-bom.csv, shrew-lite.brd, shrew-lite.sch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]
2024-08-28 added image of USB adapter cable
2024-08-28 shrew pro prototype sent off to manufacturing
    [shrew-lite.brd, shrew-lite.sch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]
2024-08-28 cosmetic tweaks to zero pcb
    [shrew-zero.brd]
2024-08-28 added led blink animations
2024-08-28 update led blink tables
2024-08-29 updated wifi LED animation documentation
2024-08-30 shrew-lite new buck vreg
    [shrew-lite.brd, shrew-lite.sch]
2024-08-30 shrew-lite buck vreg wip, shorter
    [shrew-lite.brd, shrew-lite.sch]
2024-08-30 shrew-lite another prototype order
    [shrew-lite-10-bottom_copper.GBL, shrew-lite-3-top_solderpaste.GTP, shrew-lite-4-top_soldermask.GTS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]
2024-09-01 shrew zero layout improvements
    [shrew-lite.brd, shrew-zero.brd, shrew-zero.sch]
2024-09-03 shrew zero next prototype ready to mfg
    [shrew-zero-10-bottom_copper.GBL, shrew-zero-3-top_solderpaste.GTP, shrew-zero-4-top_soldermask.GTS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]
2024-09-05 shrew zero another mfg run
    [shrew-zero.brd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]
2024-09-05 another programmer PCB
    [shrew-programmer-10-bottom_copper.GBL, shrew-programmer-3-top_solderpaste.GTP, shrew-programmer-4-top_soldermask.GTS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]
2024-09-20 shrew-pro pin silk screen label fix
    [shrew-pro.brd]
2024-09-20 shrew lite update pin labelling
    [shrew-lite.brd]
2024-10-03 easily accessible schematic images
2024-10-09 add doc explaining motor driver specs
2024-10-21 shrew-pro with additional capacitors
    [shrew-pro-10-bottom_copper.GBL, shrew-pro-3-top_solderpaste.GTP, shrew-pro-4-top_soldermask.GTS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]
2024-10-22 missed one junction (graphical change only)
    [shrew-pro.sch]
2025-02-09 updated pin map for xr2

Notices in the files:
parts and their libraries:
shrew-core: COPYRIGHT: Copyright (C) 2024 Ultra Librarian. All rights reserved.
